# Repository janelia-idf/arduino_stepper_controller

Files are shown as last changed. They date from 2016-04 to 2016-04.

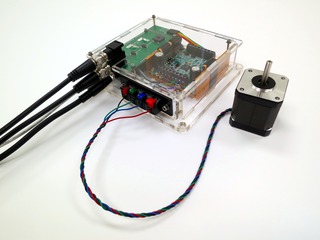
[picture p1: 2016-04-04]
images/arduino_stepper_controller_06_s.jpg

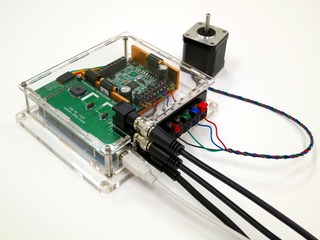
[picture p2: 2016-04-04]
images/arduino_stepper_controller_07_s.jpg

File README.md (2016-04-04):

#arduino_stepper_controller

Authors:

    Peter Polidoro <polidorop@janelia.hhmi.org>

License:

    BSD

##More Detailed Help on Installation and Usage

[modular-devices](https://github.com/janelia-modular-devices/modular-devices)

##Device Information

```json
{
  "id":"?",
  "result":{
    "device_info":{
      "name":"stepper_controller",
      "model_number":1140,
      "serial_number":0,
      "firmware_version":{
        "major":0,
        "minor":1,
        "patch":0
      }
    },
    "methods":[
      "getMemoryFree",
      "resetDefaults",
      "setSerialNumber",
      "enable",
      "disable",
      "stop",
      "getControllerInfo",
      "move",
      "playTone",
      "setToneFrequency",
      "setToneDuration",
      "setPlayToneBeforeMove",
      "setWaypointCount",
      "setWaypointTravelDuration",
      "setWaypointRepeat",
      "setWaypointRepeatPeriod"
    ]
  }
}
```

##Verbose Device Information

```json
{
  "id":"??",
  "result":{
    "device_info":{
      "name":"stepper_controller",
      "model_number":1140,
      "serial_number":0,
      "firmware_version":{
        "major":0,
        "minor":1,
        "patch":0
      }
    },
    "methods":[
      {
        "name":"getMemoryFree",
        "parameters":[],
        "result_type":"long"
      },
      {
        "name":"resetDefaults",
        "parameters":[],
        "result_type":null
      },
      {
        "name":"setSerialNumber",
        "parameters":[
          "serial_number"
        ],
        "result_type":null
      },
      {
        "name":"enable",
        "parameters":[],
        "result_type":null
      },
      {
        "name":"disable",
        "parameters":[],
        "result_type":null
      },
      {
        "name":"stop",
        "parameters":[],
        "result_type":null
      },
      {
        "name":"getControllerInfo",
        "parameters":[],
        "result_type":"object"
      },
      {
        "name":"move",
        "parameters":[],
        "result_type":null
      },
      {
        "name":"playTone",
        "parameters":[],
        "result_type":null
      },
      {
        "name":"setToneFrequency",
        "parameters":[
          "tone_frequency"
        ],
        "result_type":null
      },
      {
        "name":"setToneDuration",
        "parameters":[
          "tone_duration"
        ],
        "result_type":null
      },
      {
        "name":"setPlayToneBeforeMove",
        "parameters":[
          "play_tone_before_move"
        ],
        "result_type":null
      },
      {
        "name":"setWaypointCount",
        "parameters":[
          "waypoint_count"
        ],
        "result_type":null
      },
      {
        "name":"setWaypointTravelDuration",
        "parameters":[
          "waypoint_travel_duration"
        ],
        "result_type":null
      },
      {
        "name":"setWaypointRepeat",
        "parameters":[
          "waypoint_repeat"
        ],
        "result_type":null
      },
      {
        "name":"setWaypointRepeatPeriod",
        "parameters":[
          "waypoint_repeat_period"
        ],
        "result_type":null
      }
    ],
    "parameters":[
      {
        "name":"serial_number",
        "type":"long",
        "min":0,
        "max":65535
      },
      {
        "name":"waypoint_count",
        "type":"long",
        "min":1,
        "max":255
      },
      {
        "name":"waypoint_travel_duration",
        "units":"ms",
        "type":"long",
        "min":100,
        "max":10000
      },
      {
        "name":"tone_frequency",
        "units":"Hz",
        "type":"long",
        "min":850,
        "max":20000
      },
      {
        "name":"tone_duration",
        "units":"ms",
        "type":"long",
        "min":1,
        "max":10000
      },
      {
        "name":"play_tone_before_move",
        "type":"bool"
      },
      {
        "name":"waypoint_repeat",
        "type":"bool"
      },
      {
        "name":"waypoint_repeat_period",
        "units":"ms",
        "type":"long",
        "min":100,
        "max":10000
      }
    ]
  }
}
```

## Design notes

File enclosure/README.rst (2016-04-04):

====================================
arduino_stepper_controller enclosure
====================================

* Press eight #4 pem nuts and four #6 pem nuts into 0.25" thick base
  plate.

* Press two #6 pem nuts into 0.125" side plate.

* Attach (pcb + arduino) to 0.25" thick base plate.

* Connect a 1k resistor between IM483 P2:1 and P2:2. Connect a 1.6k
  resistor between P2:2 and P2:3.

* Attach IM483 to 0.25" thick base plate 6-32 x 1/2" socket head cap
  screws.

* Cut 4-pin 12" jumper wires 3" from connector. Separate wires back 1"
  and strip wires 1/4".

* Connect RED to IM483 P1:5, ORANGE to P1:4, YELLOW to P1:3, and
  GREEN to P1:2.

* Plug 4-pin connector to P2 on pcb.

* Set IM483 stepper resolution switch to OFF, OFF, OFF, ON, to set
  resolution to 256 microsteps/step.

* Cut UNSHIELDED 22AWG 2 COND to 3" and remove outer gray
  insulation. Solder to CONN JACK 2.5x5.5MM, RED to center, BLACK to
  terminal next to center terminal, and cut off the 3rd terminal. Cut
  wire insulation 1/8" on CONN JACK side and 1/4" on other side. Use
  3/32" x 1/2" heat shrink tubing.

* Screw CONN JACK 2.5x5.5MM into 0.125" side plate hole.

* Cut UNSHIELDED 22AWG 4 COND to 2" and remove outer gray
  insulation. BLACK: 2", GREEN: 1 7/8", WHITE: 1 3/4", RED: 1
  5/8". Cut wire insulation 1/4" on both sides. Solder to TERMINAL PB
  4CIRC 2.50" MOUNT, BLACK closest to PCB, then GREEN, then WHITE,
  then RED. With a BLUE marker, color WHITE until BLUE. Use 1/8" x
  3/4" heat shrink tubing.

* Screw TERMINAL PB 4CIRC into 0.125" side plate with two 6-32 x 3/8"
  socket head cap screws with a #6 washer on each.

* Connect TERMINAL PB 4CIRC BLACK to P2:5, GREEN to P2:6, BLUE to
  P2:7, and RED to P2:8.

* Connect CONN JACK BLACK to PCB P3:GND and CONN JACK RED to PCB
  P3:+24VDC.

* Cut another UNSHIELDED 22AWG 2 COND to 3" and remove
  insulation. Connect BLACK to PCB P3:GND and RED to PCB P3:+24VDC.

* Connect BLACK to IM483 P2:3 and RED to IM483 P2:4.

* Place colored tape on spring terminal tops, BLACK, GREEN, and
  BLUE. (the RED terminal is already RED).

Author: Peter Polidoro

This program is free software: you can redistribute it and/or modify
it under the terms of the GNU Lesser General Public License as published by
the Free Software Foundation, either version 3 of the License, or
(at your option) any later version.

This program is distributed in the hope that it will be useful,
but WITHOUT ANY WARRANTY; without even the implied warranty of
MERCHANTABILITY or FITNESS FOR A PARTICULAR PURPOSE.  See the
GNU Lesser General Public License for more details.

You should have received a copy of the GNU Lesser General Public License
along with this program.  If not, see <http://www.gnu.org/licenses/>.

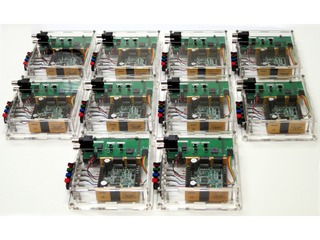
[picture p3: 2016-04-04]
images/arduino_stepper_controller_08_s.jpg

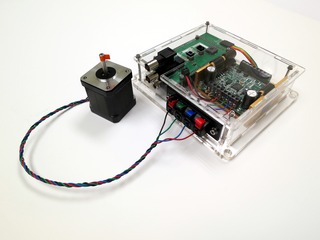
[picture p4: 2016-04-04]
images/arduino_stepper_controller_11_s.jpg

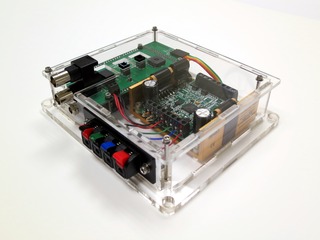
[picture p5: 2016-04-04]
images/arduino_stepper_controller_09_s.jpg

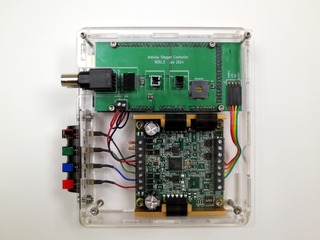
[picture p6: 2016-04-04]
images/arduino_stepper_controller_10_s.jpg

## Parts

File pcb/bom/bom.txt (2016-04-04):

-*- mode:org -*-

# Opt101.lst
| ref     | value                    |
|---------+--------------------------|
| C1      | 10uF                     |
| C2      | 10uF                     |
| C3      | 0.1uF                    |
| P1      | DBNC_INPUT               |
| P2      | DRIVE                    |
| P3      | +24VDC                   |
| P4      | INT_STEPPER              |
| P5      | INT_TONE                 |
| R1      | 118                      |
| REG1    | CONV_DC_DC               |
| SHIELD1 | ARDUINO_MEGA_SHIELD_FULL |
| SP1     | SPEAKER                  |
| U1      | MAX6817                  |
|         |                          |

# Bill of Materials
| ! | part    | description                                                     | vendor             | part number       | quantity |   cost |
|---+---------+-----------------------------------------------------------------+--------------------+-------------------+----------+--------|
|   | PCB     | arduino_stepper_controller                                      | pcbuniverse        | v1.4              |        1 |   1.00 |
|   | C1-2    | CAP CER 10UF 50V 10% X7S 1210                                   | digikey            | 445-4536-1-ND     |        3 |   1.24 |
|   | C3      | CAP CER 0.1UF 50V 10% X7R 1210                                  | digikey            | 478-3586-1-ND     |        1 |   0.39 |
|   | P1      | CONN BNC JACK R/A 75 OHM PCB                                    | digikey            | ACX1655-ND        |        1 |  11.10 |
|   | P2      | CONN HEADER 4POS .100 R/A 30AU                                  | digikey            | 609-3312-ND       |        1 |   0.40 |
|   | P2      | Jumper Wire - 0.1", 4-pin, 12"                                  | sparkfun           | PRT-10374         |        1 |   1.95 |
|   | P2      | IM483 microstepping driver                                      | schneider-electric | im483             |        1 |   1.00 |
|   | P3      | POWER SUPPLY SWITCHER 78W 24V                                   | digikey            | 271-2777-ND       |        1 |  63.84 |
|   | P3      | LINE CORD 3 COND US                                             | digikey            | 993-1039-ND       |        1 |   3.18 |
|   | P3      | TERMINAL BLOCK 3.5MM 2POS PCB                                   | digikey            | ED1514-ND         |        1 |   0.63 |
|   | P4-5    | CONN HEADER 2POS .100 VERT GOLD                                 | digikey            | WM4800-ND         |        2 |   0.88 |
|   | P4-5    | UNSHIELDED 22AWG 2 COND                                         | digikey            | W120-100-ND       |        1 |   0.20 |
|   | P4-5    | CONN HOUSING 2POS .100 W/LATCH                                  | digikey            | WM2900-ND         |        4 |   0.49 |
|   | P4-5    | CONN HOUSING MALE 2POS .100                                     | digikey            | WM2533-ND         |        2 |   0.79 |
|   | P4-5    | CONN TERM FEMALE 22-24AWG GOLD                                  | digikey            | WM2570-ND         |        8 |   0.34 |
|   | P4-5    | CONN TERM MALE 22-24AWG GOLD                                    | digikey            | WM2567-ND         |        4 |   0.37 |
|   | P4-5    | Pendant Switch with Cable, Push-Button, 1 NO, 5 Amps at 120V AC | mcmaster           | 6944K11           |        2 |  18.89 |
|   | R1      | RES 118 OHM 1/2W 1% 1210 SMD                                    | digikey            | P118AACT-ND       |        1 |   0.51 |
|   | REG1    | CONV DC/DC 1A 12V OUT SIP VERT                                  | digikey            | 945-1392-5-ND     |        1 |   8.79 |
|   | SHIELD1 | BOARD MCU MEGA2560                                              | digikey            | 1050-1018-ND      |        1 |  51.91 |
|   | SHIELD1 | CONN HDR VERT 50POS .100" SNGL                                  | digikey            | SAM1055-50-ND     |        2 |   3.42 |
|   | SP1     | SPEAKER 8OHM .7W 88DB 13MM SMD                                  | digikey            | 668-1259-1-ND     |        1 |   8.18 |
|   | U1      | IC DEBOUNCER SWITCH DUAL SOT23-6                                | digikey            | MAX6817EUT+TCT-ND |        1 |   5.25 |
|---+---------+-----------------------------------------------------------------+--------------------+-------------------+----------+--------|
| # | total   |                                                                 |                    |                   |          | 215.78 |
#+TBLFM: @25$7=(@I$quantity..@II$quantity)*(@I$cost..@II$cost);%.2f;N

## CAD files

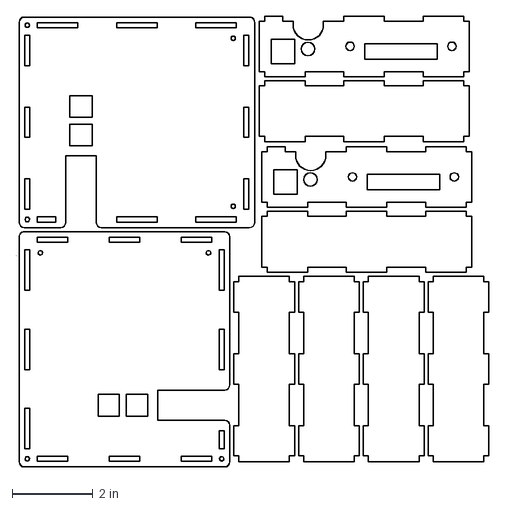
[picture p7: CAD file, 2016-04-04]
enclosure/arduino_enclosure_stepper_controller.125in.array.dxf
11.7 x 11.1 in

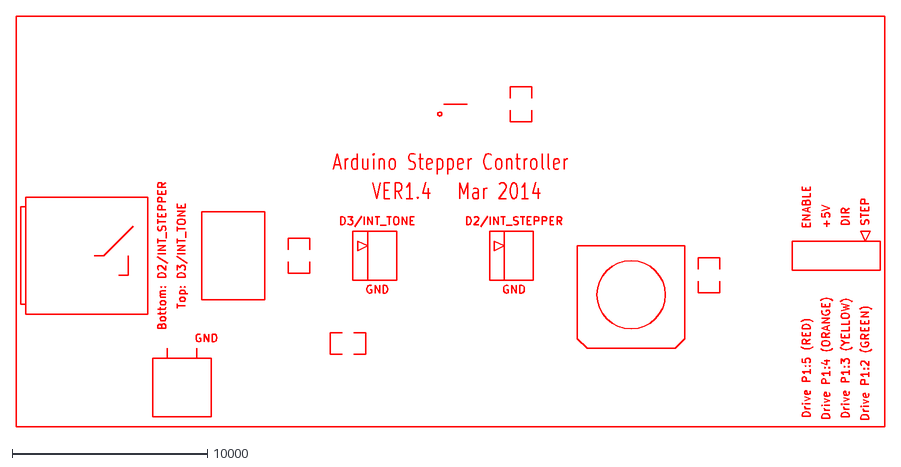
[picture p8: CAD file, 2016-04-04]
pcb/v1.4/dxf/arduino_stepper_controller-SilkS_Front.dxf
44500.0 x 21000.0

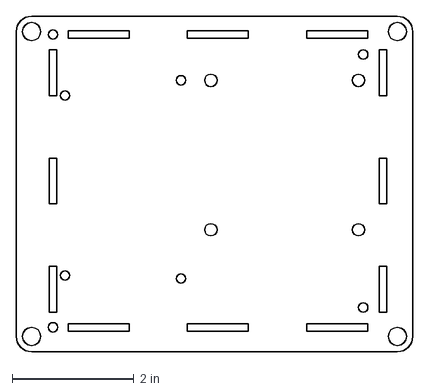
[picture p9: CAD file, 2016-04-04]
enclosure/arduino_enclosure_stepper_controller.25in.dxf
6.50 x 5.50 in

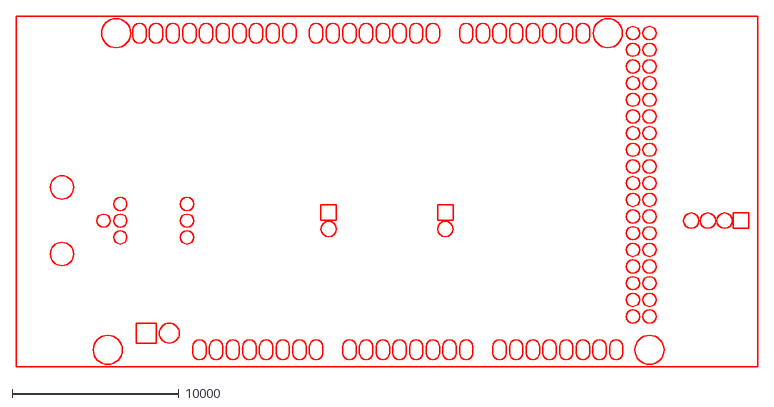
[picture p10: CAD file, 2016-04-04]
pcb/v1.4/dxf/arduino_stepper_controller-Mask_Back.dxf
44500.0 x 21000.0

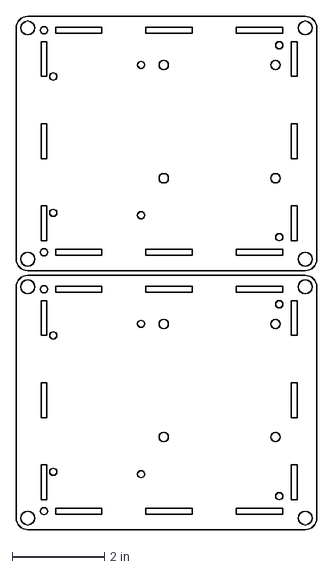
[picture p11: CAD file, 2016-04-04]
enclosure/arduino_enclosure_stepper_controller.25in.array.dxf
6.50 x 11.1 in

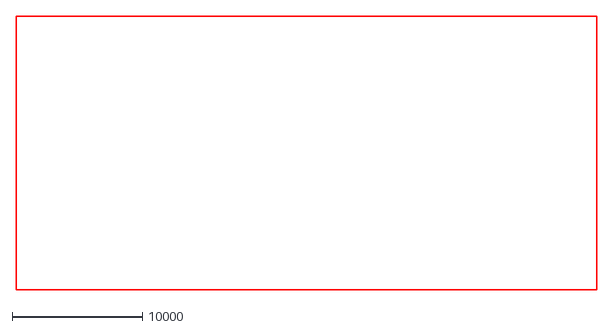
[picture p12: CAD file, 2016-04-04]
pcb/v1.4/dxf/arduino_stepper_controller-SilkS_Back.dxf
44500.0 x 21000.0

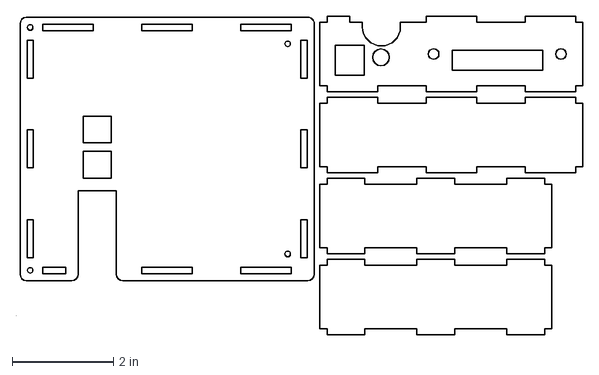
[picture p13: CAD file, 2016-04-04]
enclosure/arduino_enclosure_stepper_controller.125in.dxf
11.2 x 6.30 in

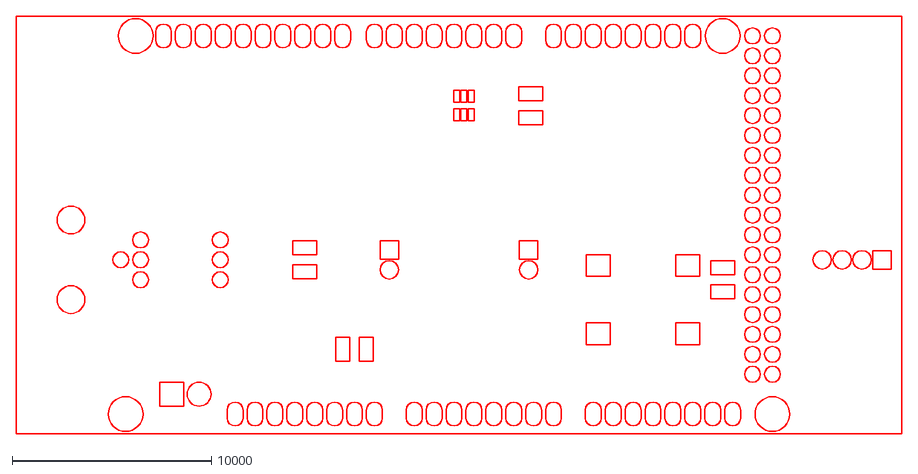
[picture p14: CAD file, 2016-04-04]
pcb/v1.4/dxf/arduino_stepper_controller-Mask_Front.dxf
44500.0 x 21000.0

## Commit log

2016-04-04 Initial commit.
    [$savepcb.brd, arduino_enclosure_stepper_controller.125in.array.dxf, arduino_enclosure_stepper_controller.125in.dxf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]
2017-01-03 Removed firmware/stepper_controller.
